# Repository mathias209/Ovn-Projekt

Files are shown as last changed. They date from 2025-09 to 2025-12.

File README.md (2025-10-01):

# Repo til vores ovnprojekt
beskrivelse go here

rapporter ligger i onedrive
rapport i word er her:
[Rapport](https://dtudk-my.sharepoint.com/:w:/r/personal/s256053_dtu_dk/Documents/Desktop/Projects/Ovn%20project.docx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)

[link til gruppe arbejde i Stens timer](https://github.com/mathias209/Elektroteknik-gruppearbejde)

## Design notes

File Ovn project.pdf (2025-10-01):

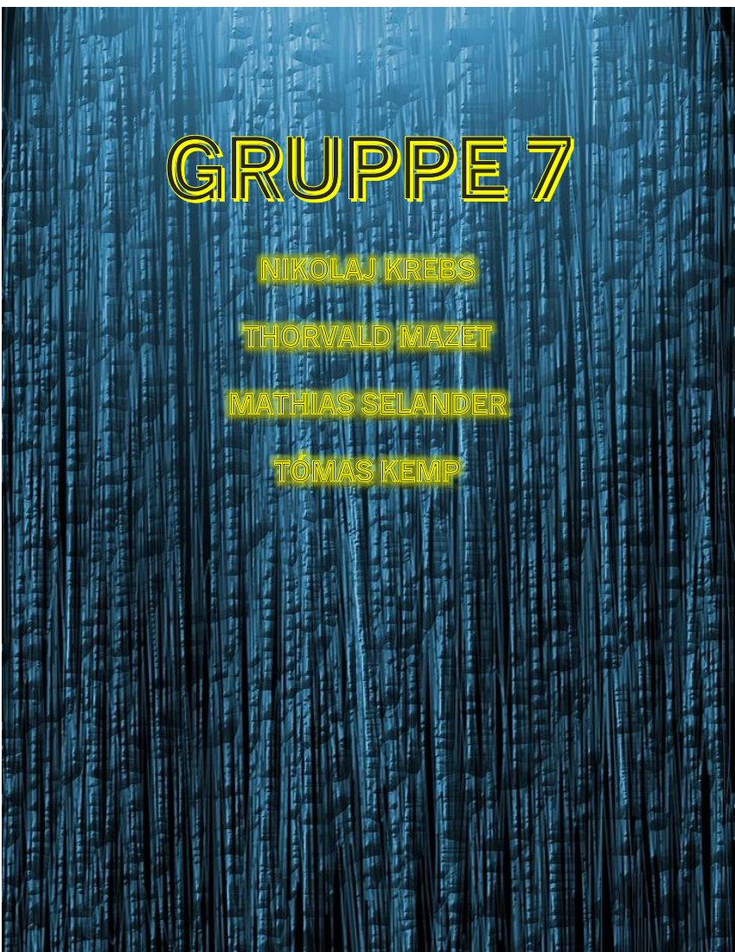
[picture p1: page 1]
01/10-2025 Gruppe 7

## Rapport for Digital Oscillator

# Contents

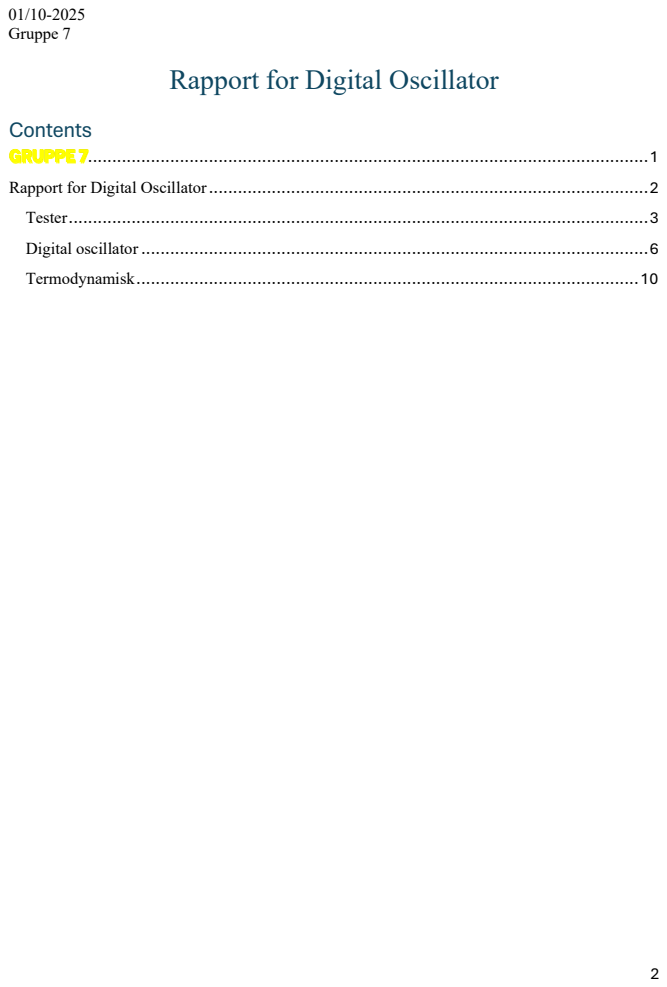
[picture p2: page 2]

## Tester

Tegn et lille diagram med en Light Emitting diode (LED) i serieforbindelse med en modstand.

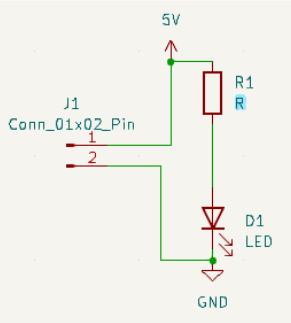
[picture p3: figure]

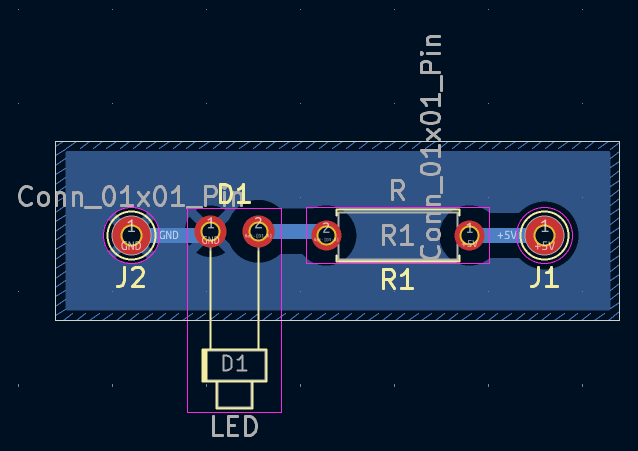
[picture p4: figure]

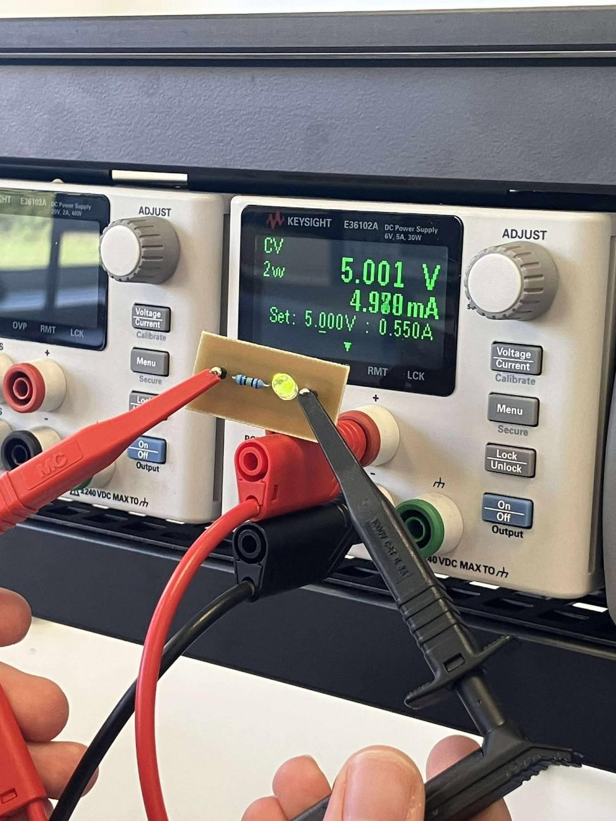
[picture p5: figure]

Iled = 5mA

VS = 5V

VR = 3V

R =

3V
0.005A

= 600Ω

Vi skal bruge en 600 ohm resistor.

## Digital oscillator

Vi skal lave et pcb-board med følgende kredsløb:

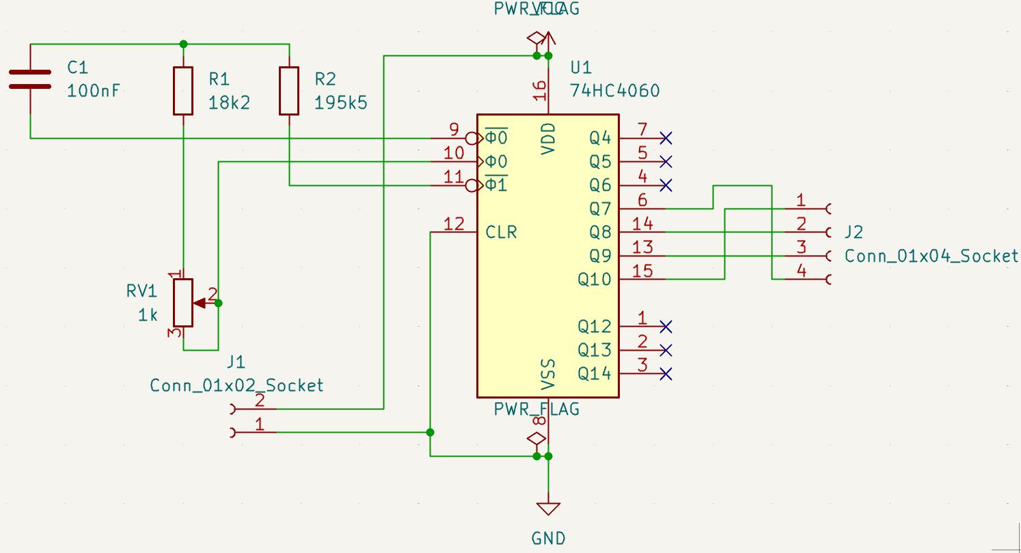
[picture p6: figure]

Vores færdige PCB kom så til at se sådan ud:

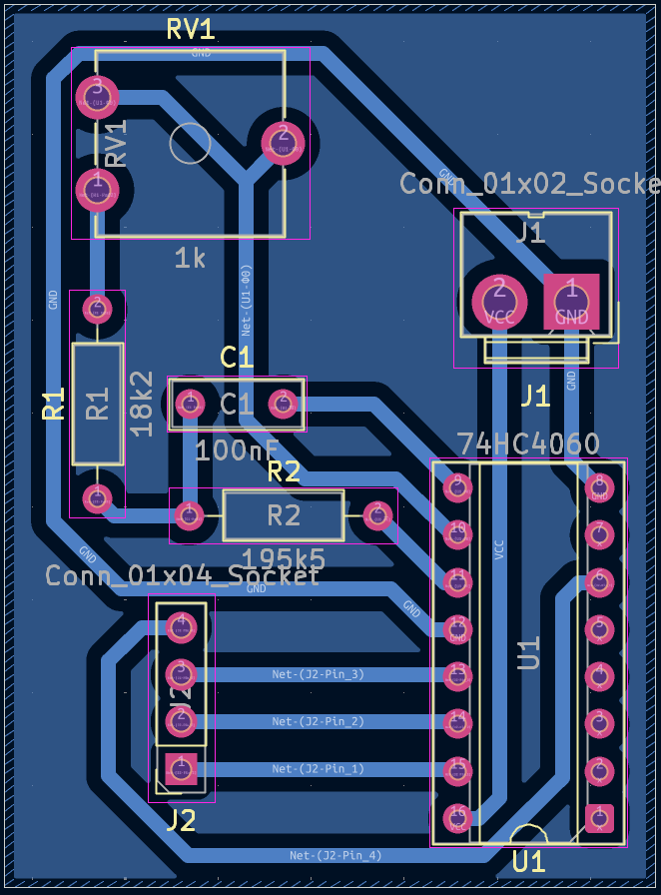
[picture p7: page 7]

Vi skulle udregne modstanden R1 så det var en indgangsfrekvens på 256Hz. Det gjorde vi med følgende formel:

1

Udregning i Maple:

I serie med modstanden skulle vi have et potentiometer så vi kunne justere vores modstand til at være så præcis så muligt. Den totale modstand skulle maksimalt være 10% højere en værdien som vi udregnet:

For at ramme de 17k8 ohm præcist, tilslutter vi en modstand på 17k2 ohm samt et potentiometer på 1k ohm.

Herefter har vi sat modstanden plus potentiometer gennem et multimeter og målt mens vi har drejet potentiometeret til at multimeteret viste 17k8 ohm.

Herefter tjekker vi frekvensen fra udgang Q8 gennem et ocsilloscop og ser en frekvens på 0.91 hz. Vores teori er at fejlen på 0.09hz sker pga. loddetin der virker som mindre capacitator.

1 Formel fra opgavebeskrivelse.

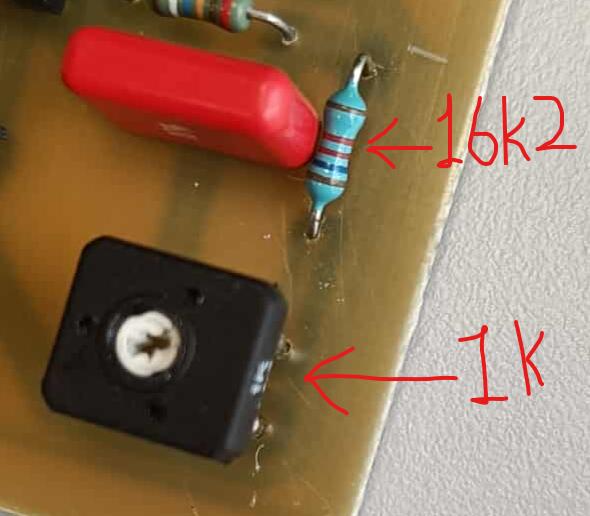
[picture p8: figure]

For at ramme vores ønskede frekvens på 1 hz ud fra udgang Q8, må vi derfor installere en mindre modstand i stedet for 17k2 ohm. Vi har ændret modstanden til at være 16k2 ohm. Vi har herefter drejet på potentiometeret til at vi får en frekvens på 0.99hz.

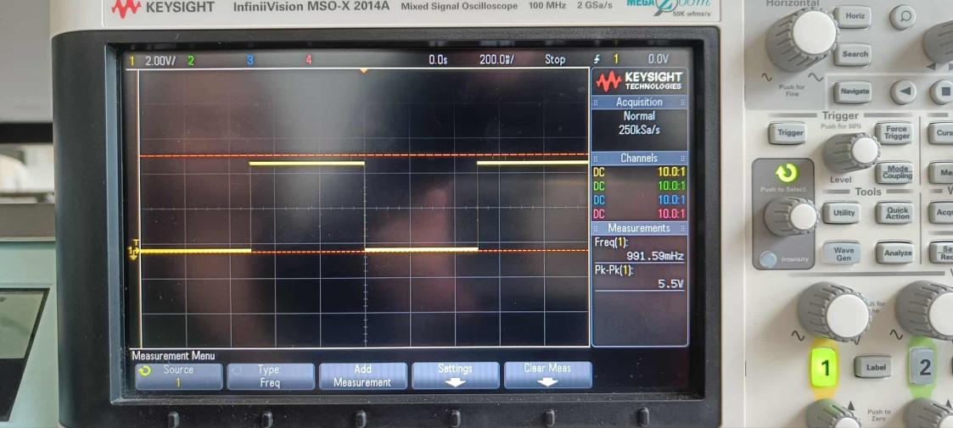
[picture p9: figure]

Herefter har vi målt på vores modstand gennem multimeter:

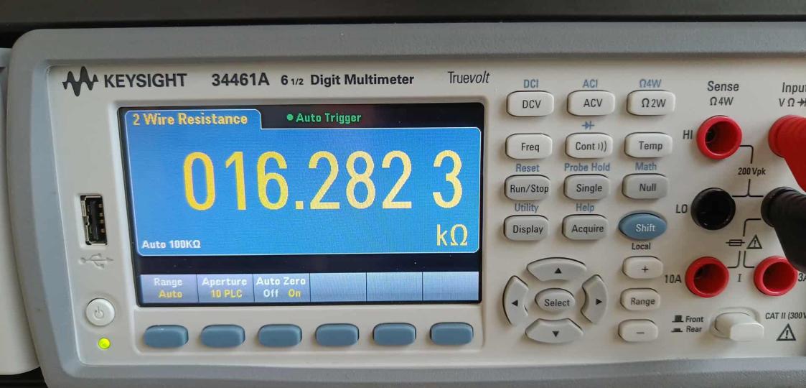
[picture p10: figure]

Her ser vi at vores samlede modstand R1 ligger på 16.28 kOhm.

## Termodynamisk

Vores udregning for R3 for henholdsvis 5W og 10W:

2

2

Screenshot af excel fil fra projektmappe.

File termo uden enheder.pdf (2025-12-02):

## Termodynamisk data

:

## Udregning af målt temp LM35DT

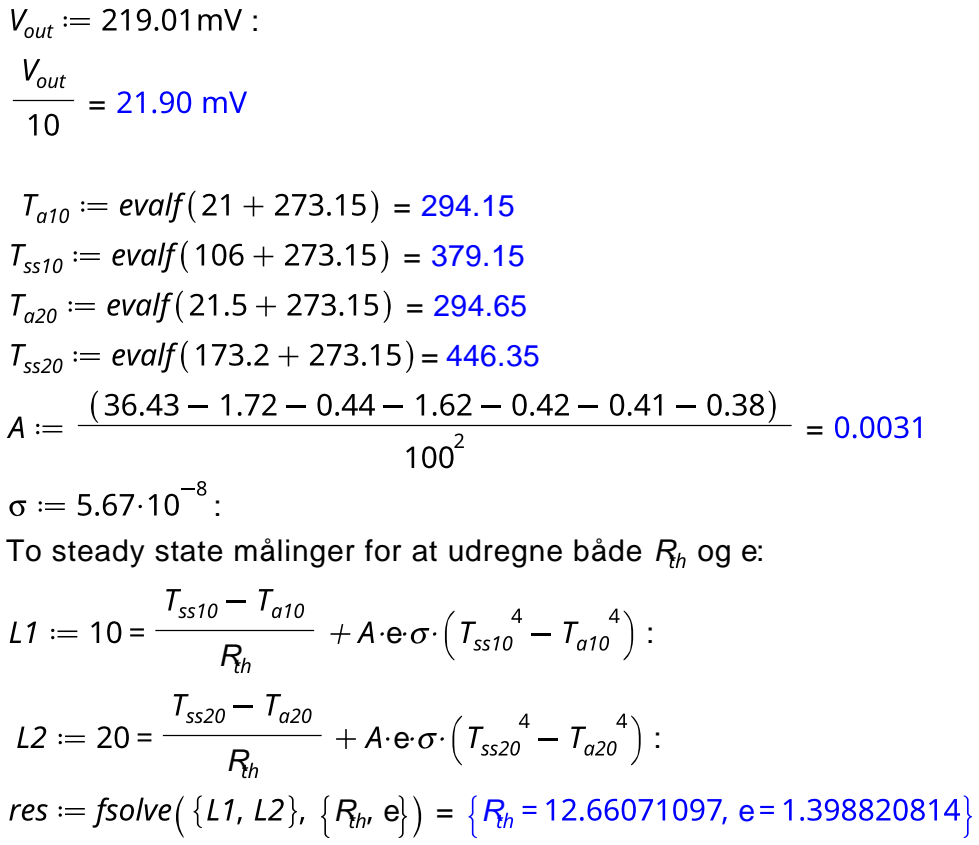
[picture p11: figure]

To steady state målinger for at udregne både R og e:

Siden e ikke mindst ikke har en passende værdi, den er ikke engang mellem 0 og 1. Derfor er det rimelig sikkert at gå ud fra at vores målinger ikke er præcise nok. Derfor antager vi en rimelig værdi for e på 0.25, og udregner en R for begge vores målinger og

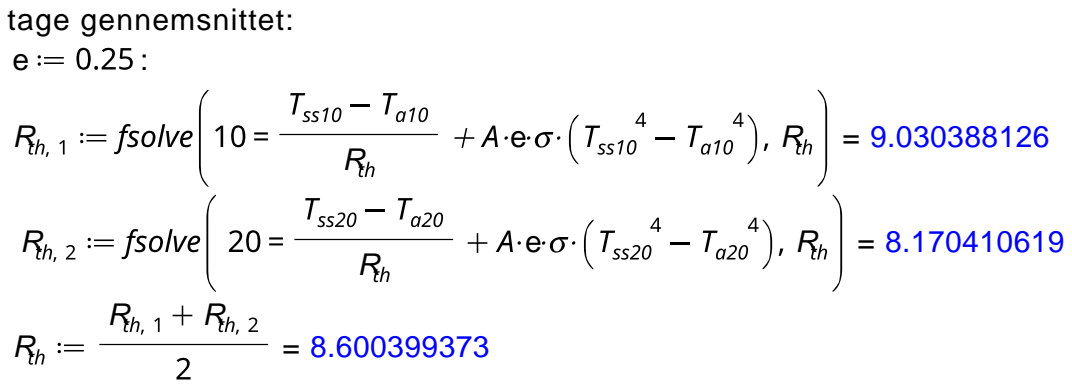
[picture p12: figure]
tage gennemsnittet:

## Cth

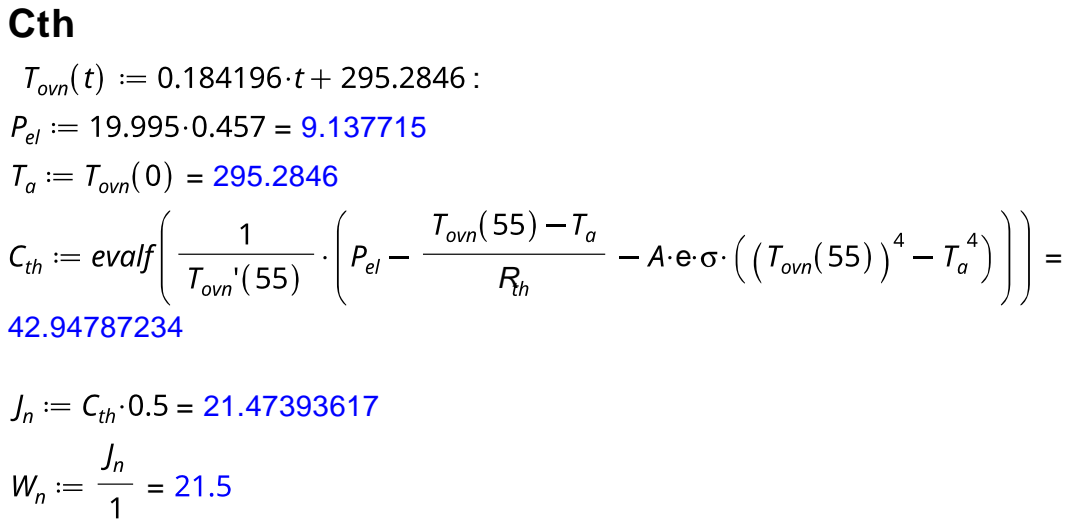
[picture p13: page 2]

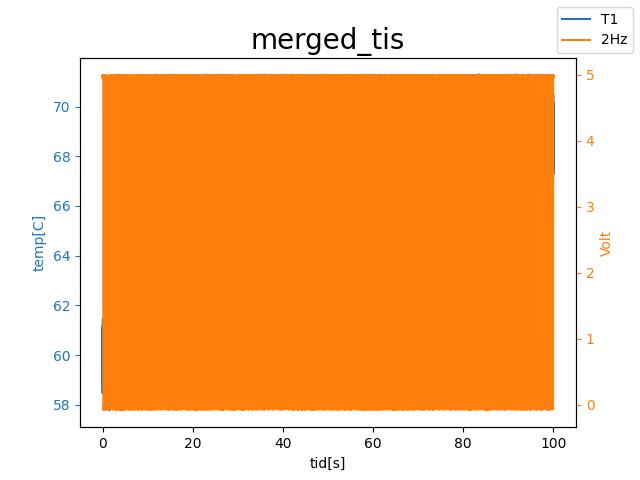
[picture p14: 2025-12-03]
python datahåndtering/merged_tis-out.jpg

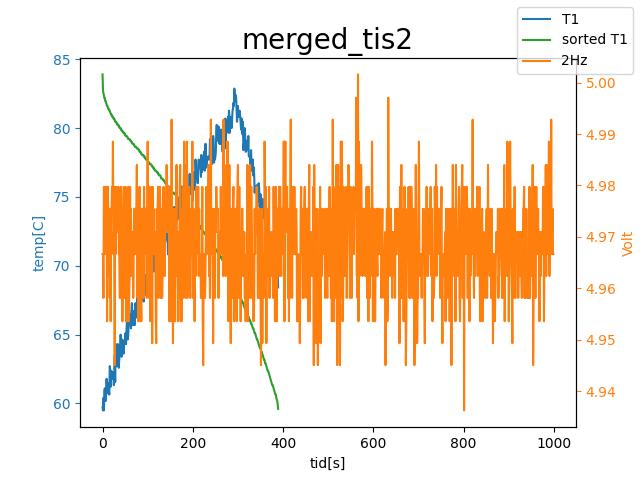
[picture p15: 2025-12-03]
python datahåndtering/merged_tis2-out.jpg

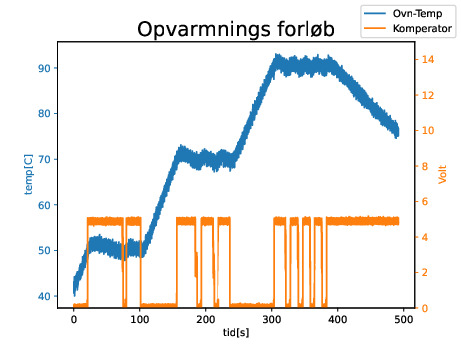
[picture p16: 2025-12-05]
python datahåndtering/Opvarmnings forløb.jpg

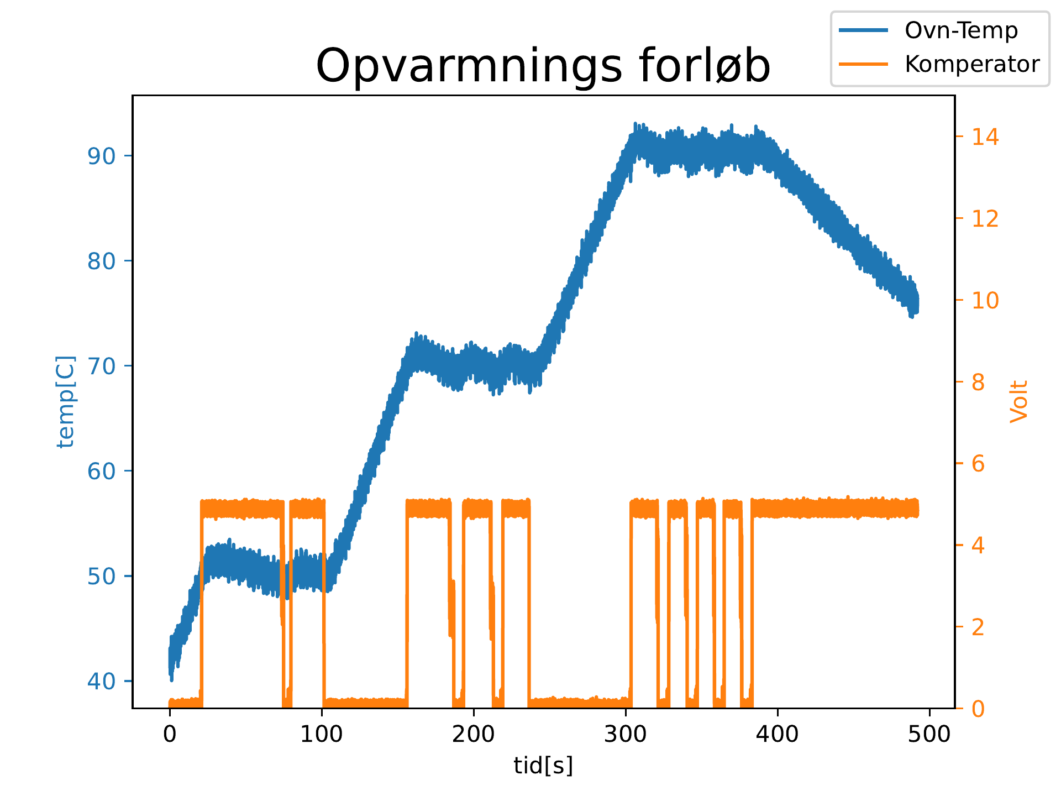
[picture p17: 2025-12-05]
python datahåndtering/output-1.png

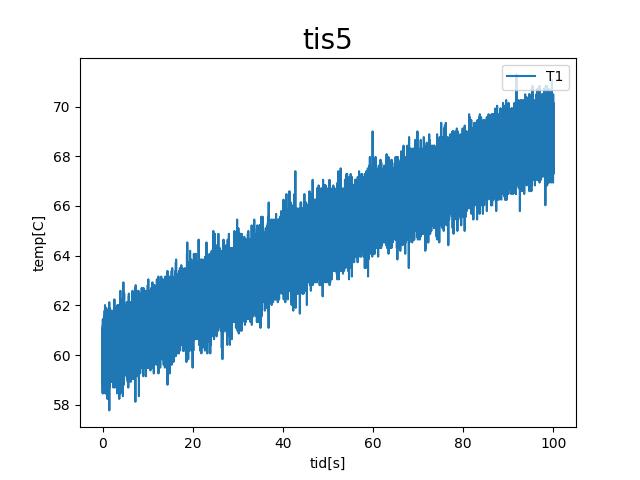
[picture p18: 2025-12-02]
python datahåndtering/tis5-out.jpg

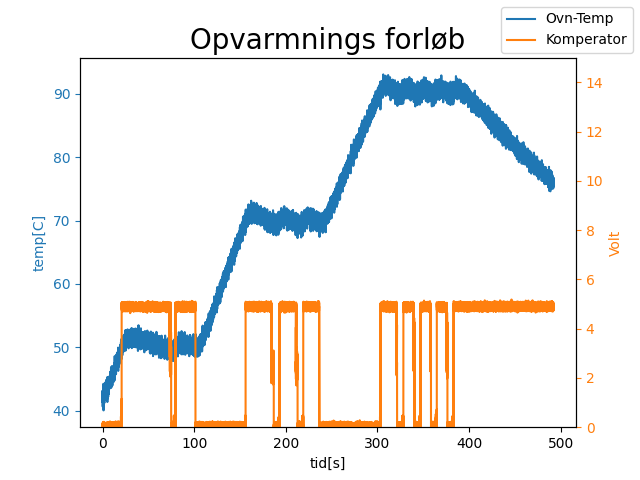
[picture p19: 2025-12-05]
python datahåndtering/Opvarmnings forløb.png

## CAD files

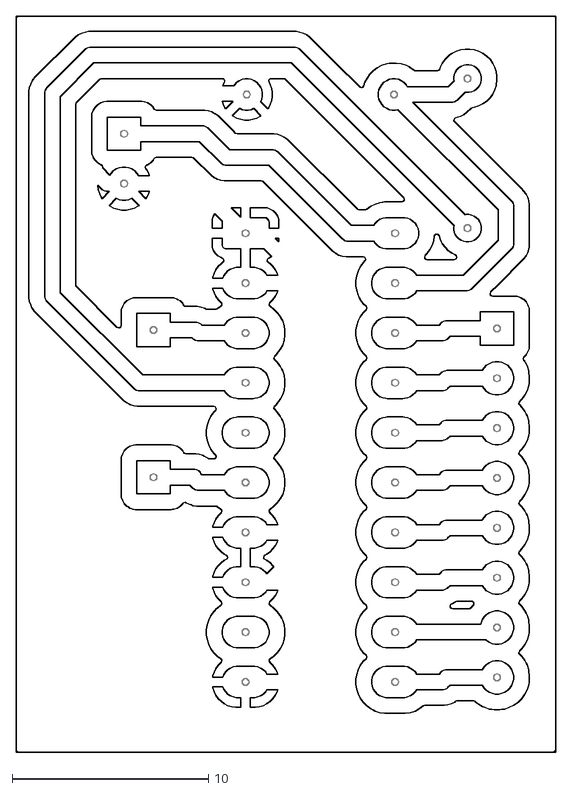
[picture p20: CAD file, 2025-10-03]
adc/ADC-B_Cu.dxf
27.5 x 37.5

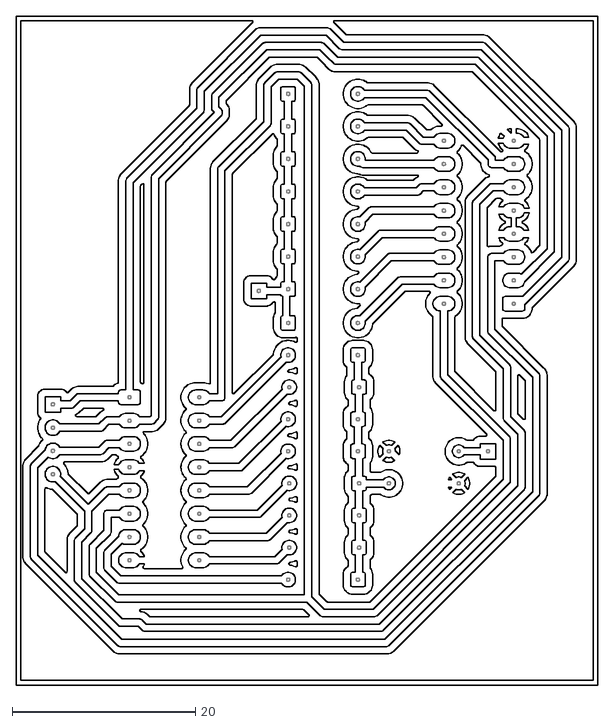
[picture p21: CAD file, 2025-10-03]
decoder/decoder-B_Cu.dxf
63.5 x 73.0

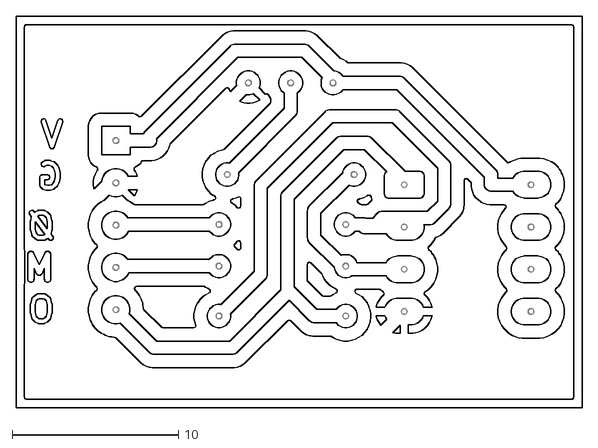
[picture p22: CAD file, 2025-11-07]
Differens forstærker/Differens forstærker-B_Cu.dxf
34.0 x 23.5

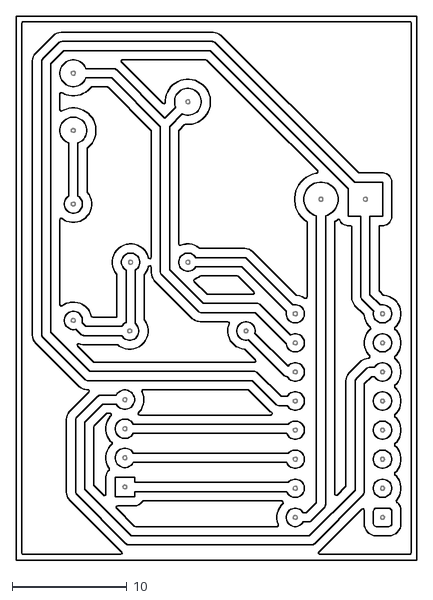
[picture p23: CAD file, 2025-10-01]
digital oscilatoropgave 2/digital oscilatoropgave 2-B_Cu.dxf
35.0 x 47.5

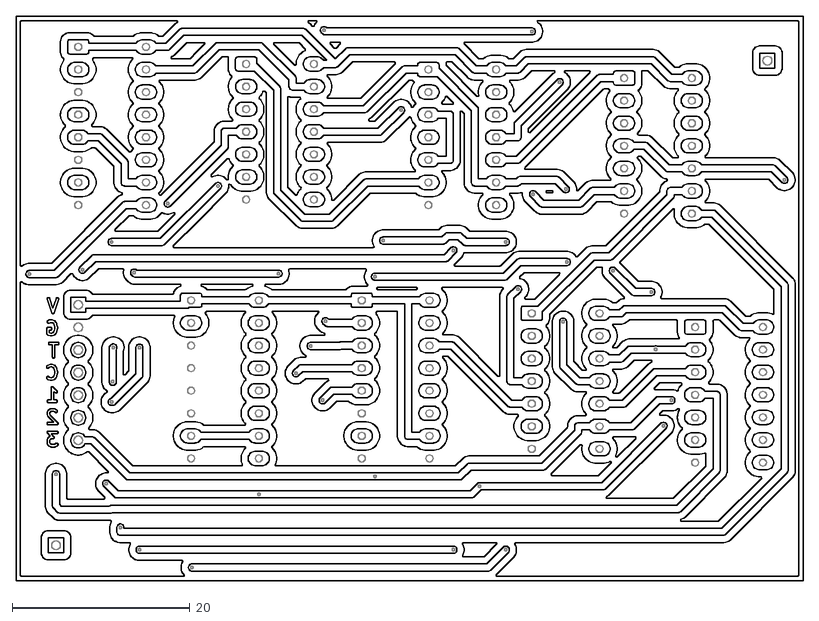
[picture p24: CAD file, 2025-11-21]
digital styring/digital styring-B_Cu.dxf
88.5 x 63.5

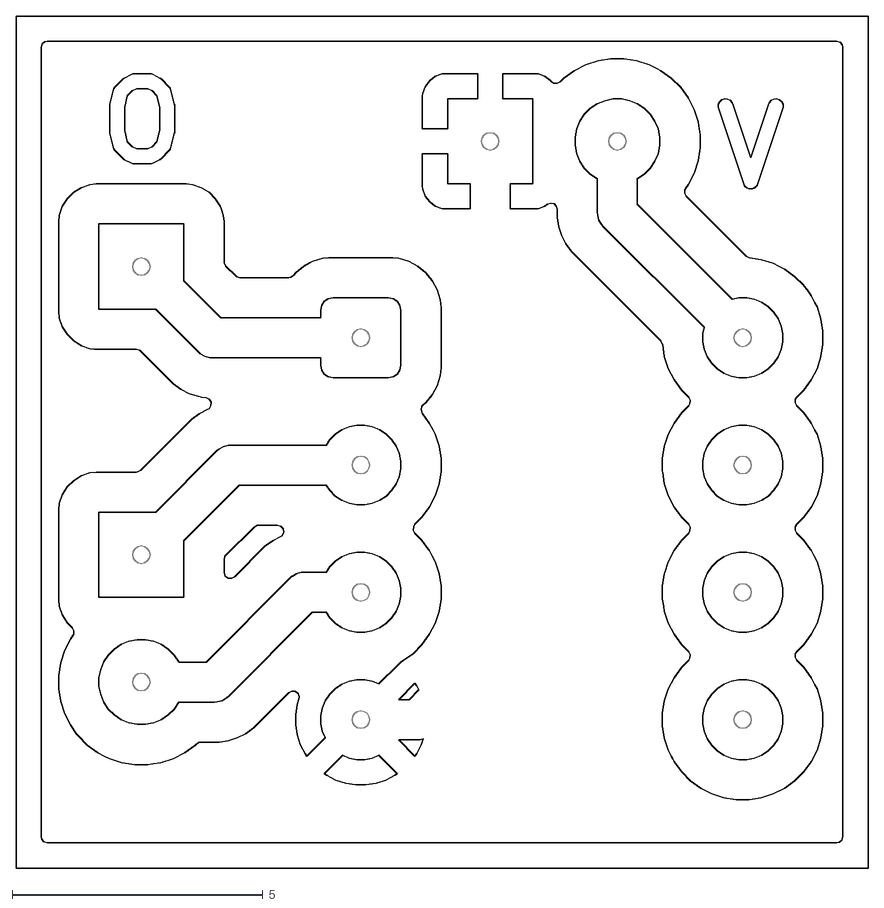
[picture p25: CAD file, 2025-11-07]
Komparator/komparator-B_Cu.dxf
17.0 x 17.0

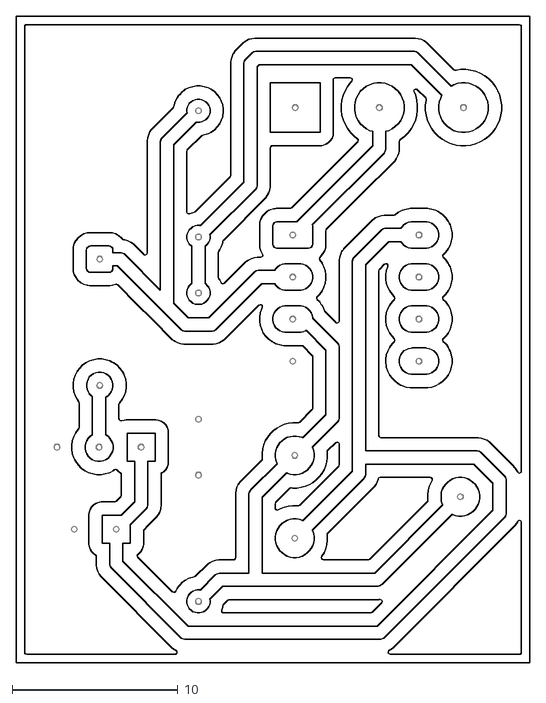
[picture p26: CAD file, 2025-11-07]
Måling af termodynamisk data/Måling af termodynamisk data-B_Cu.dxf
31.0 x 39.0

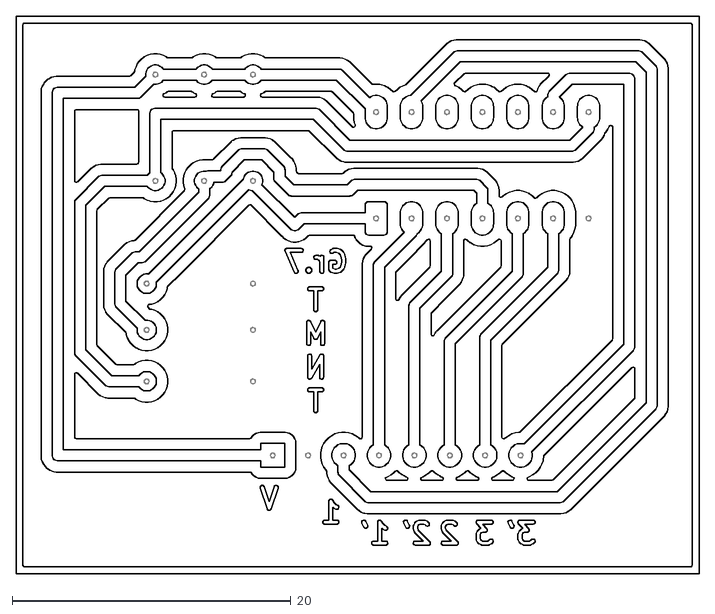
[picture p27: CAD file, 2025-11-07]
Spændingsdeler multiplexer/Spændingsdeler multiplexer-B_Cu.dxf
49.0 x 40.0

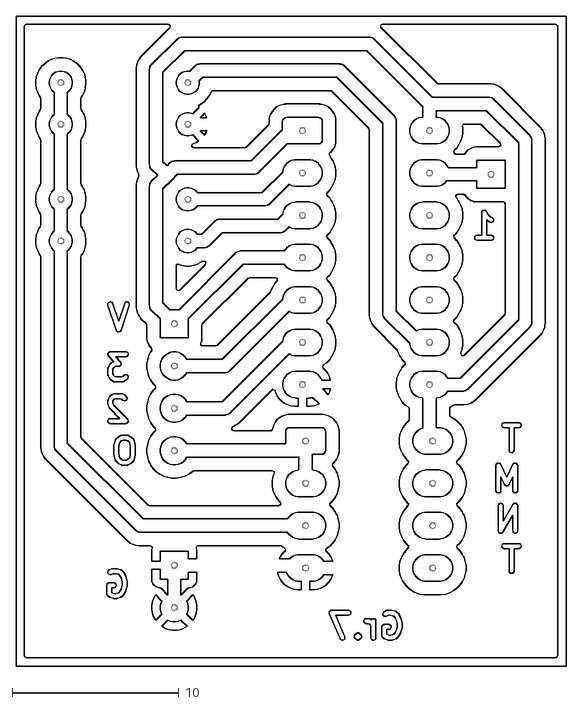
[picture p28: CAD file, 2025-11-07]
Spændingsdeler/Spændingsdeler-B_Cu.dxf
33.0 x 39.0

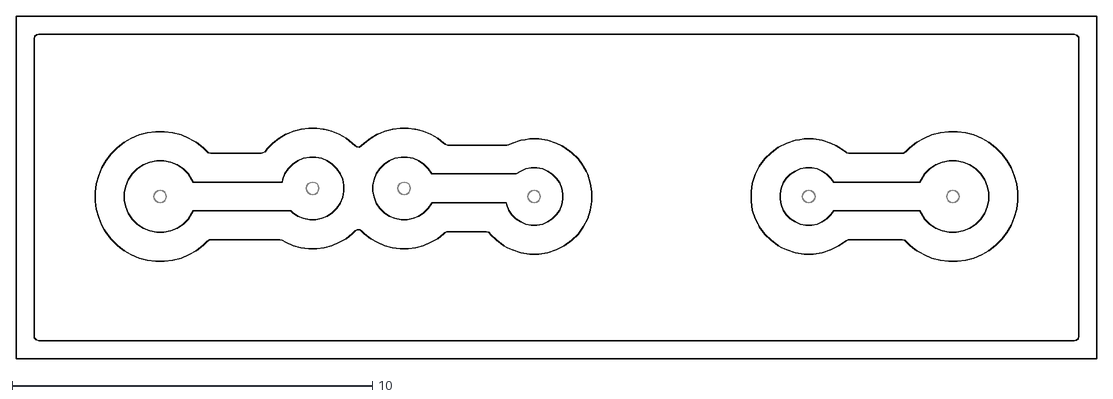
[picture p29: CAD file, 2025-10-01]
tester/tester-B_Cu.dxf
30.0 x 9.50

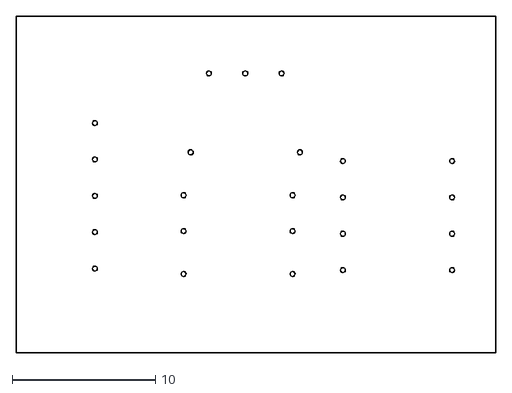
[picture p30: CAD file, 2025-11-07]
Differens forstærker/Differens forstærker-Edge_Cuts.dxf
33.5 x 23.5

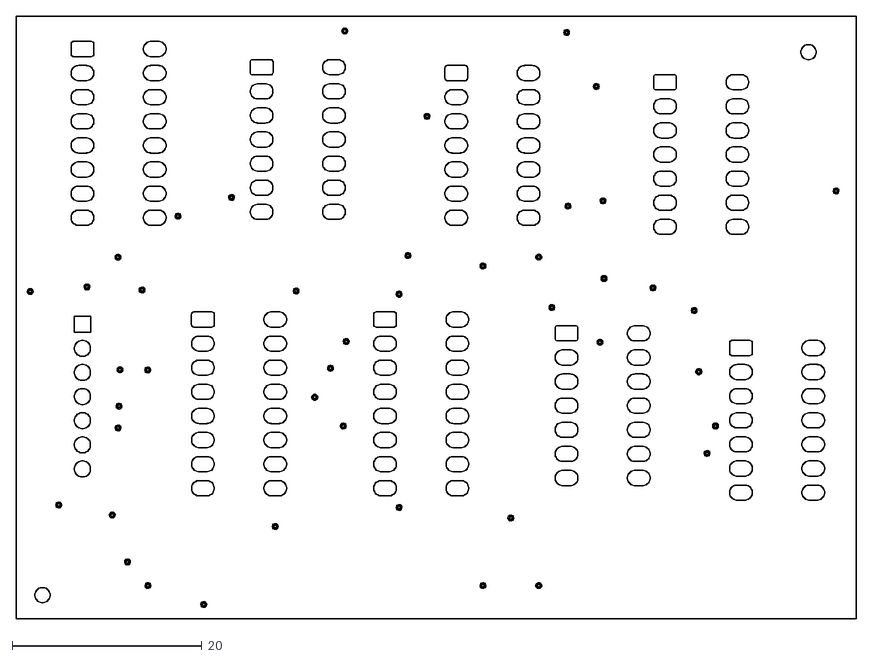
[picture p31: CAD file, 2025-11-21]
digital styring/digital styring-In1_Cu.dxf
88.5 x 63.5

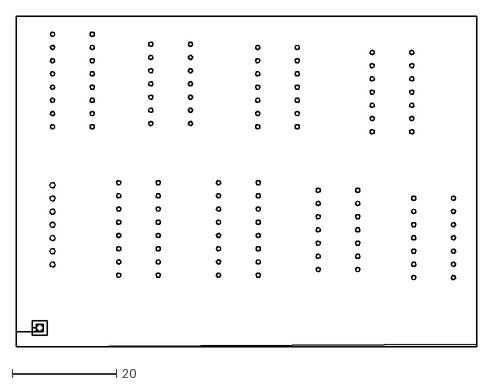
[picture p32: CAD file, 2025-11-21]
digital styring/digital styring-User_Comments.dxf
88.5 x 63.5

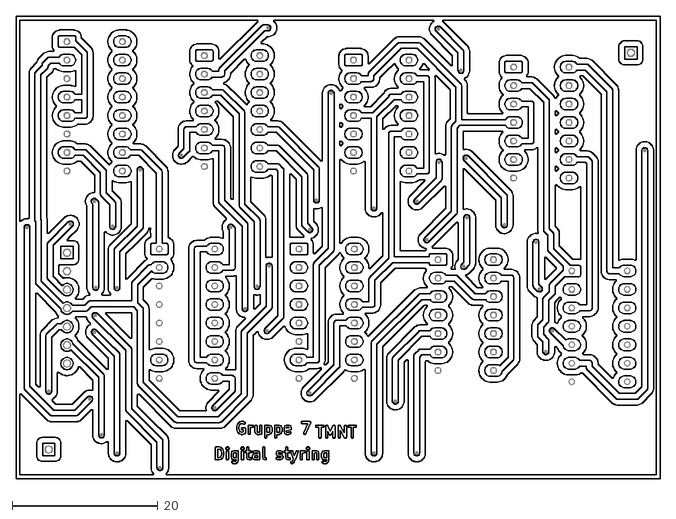
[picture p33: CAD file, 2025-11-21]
digital styring/digital styring-F_Cu.dxf
88.5 x 63.5

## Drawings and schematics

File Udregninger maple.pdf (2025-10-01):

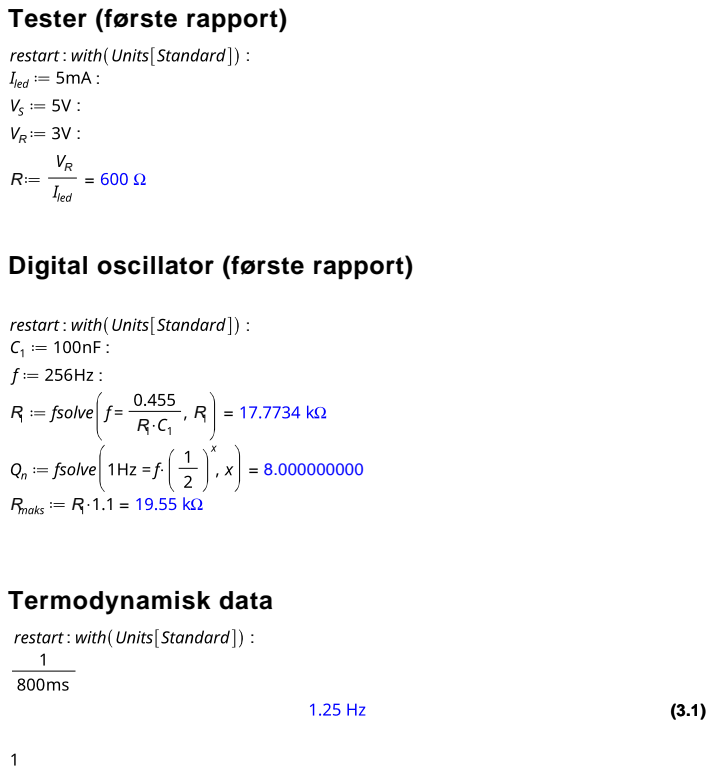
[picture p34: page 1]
Termodynamisk data

Tester (første rapport)

Digital oscillator (første rapport)

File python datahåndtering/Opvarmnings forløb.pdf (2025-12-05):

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

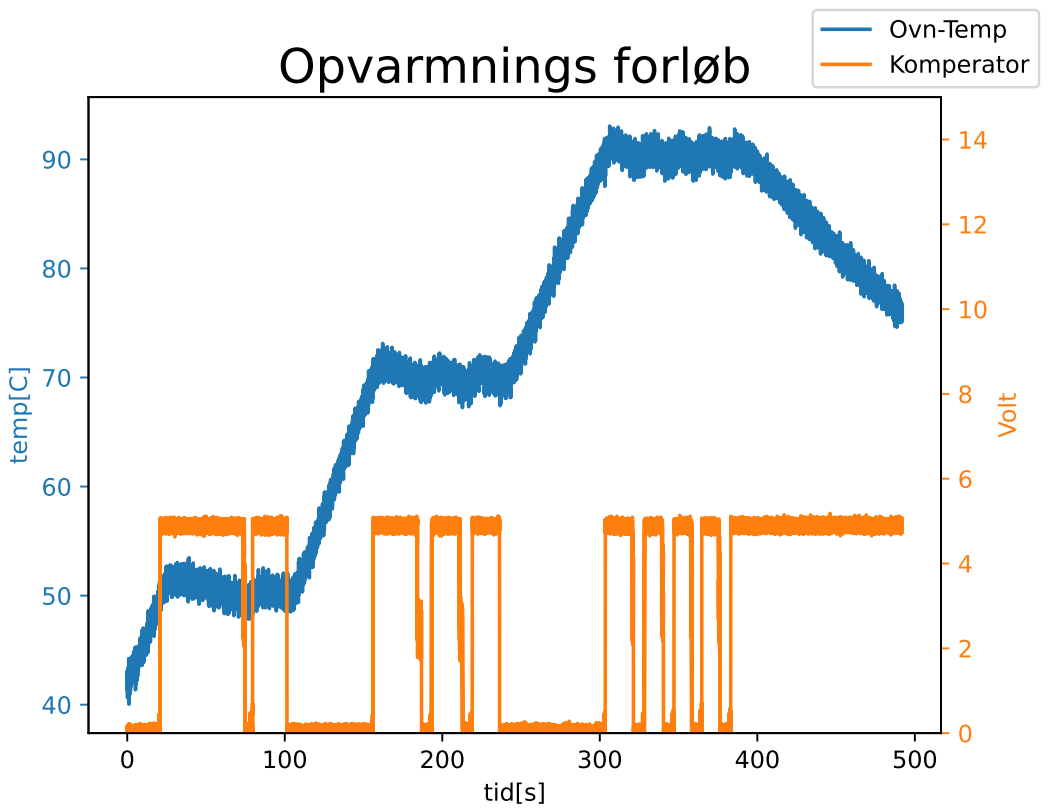
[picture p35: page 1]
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

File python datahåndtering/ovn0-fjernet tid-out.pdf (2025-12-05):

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

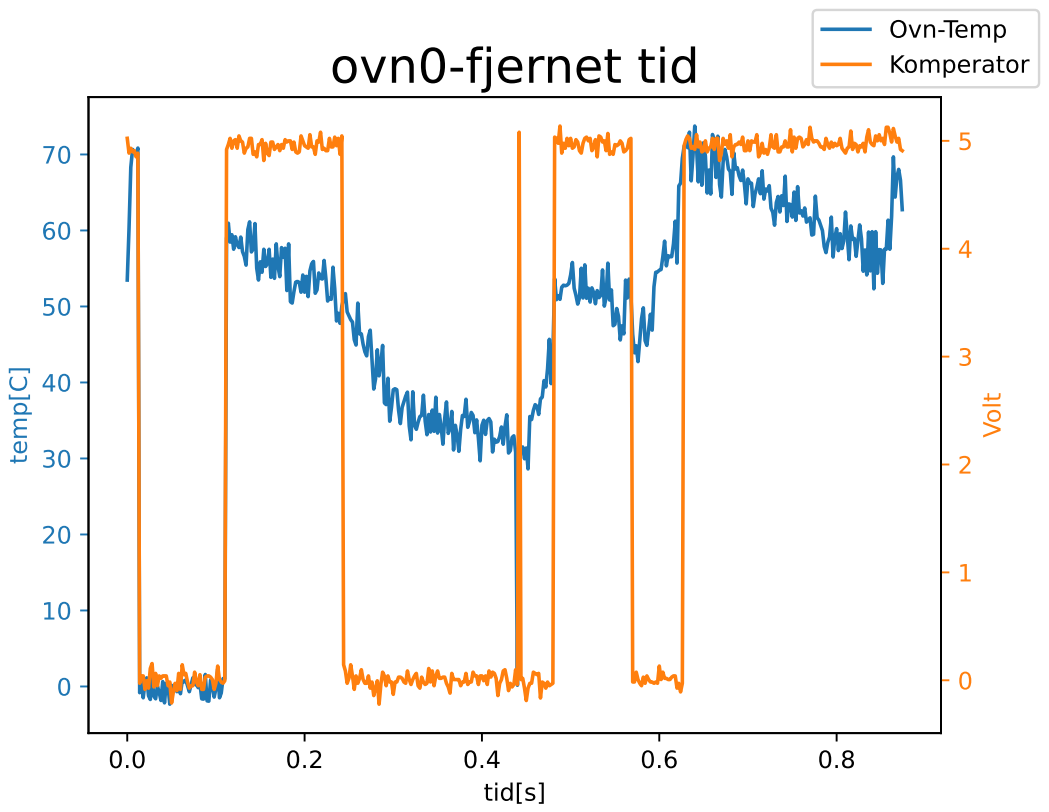
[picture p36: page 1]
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

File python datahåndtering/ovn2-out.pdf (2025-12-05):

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

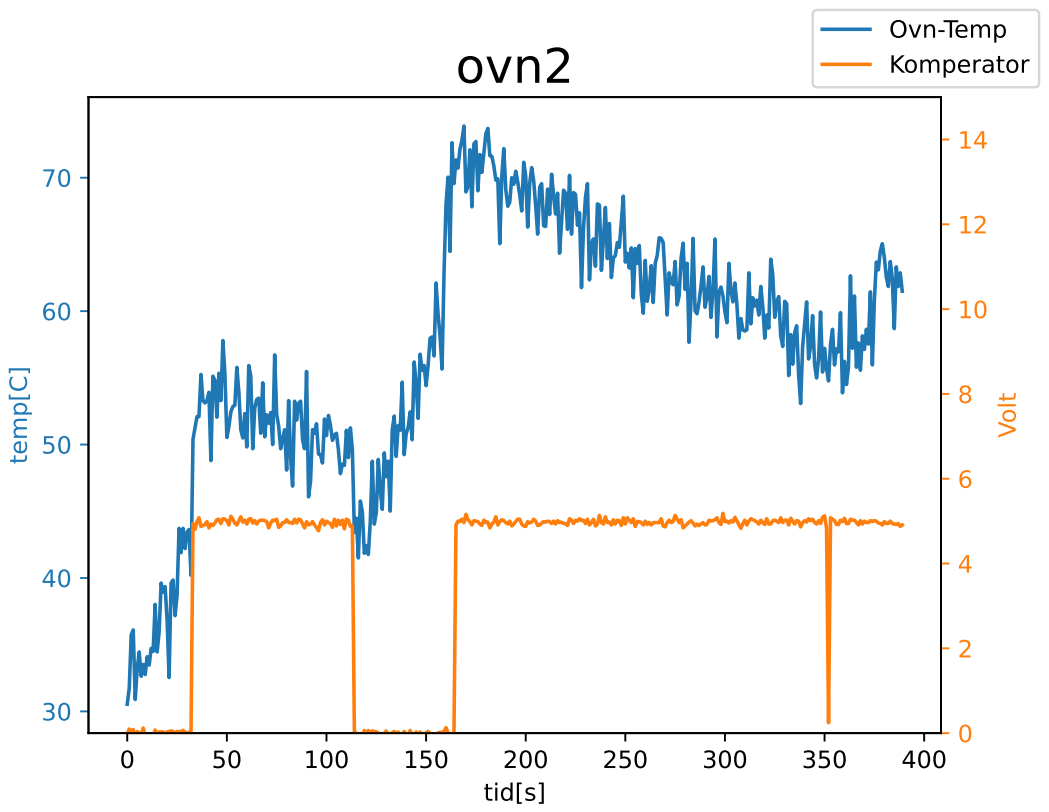
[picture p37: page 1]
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

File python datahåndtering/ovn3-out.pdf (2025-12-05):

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

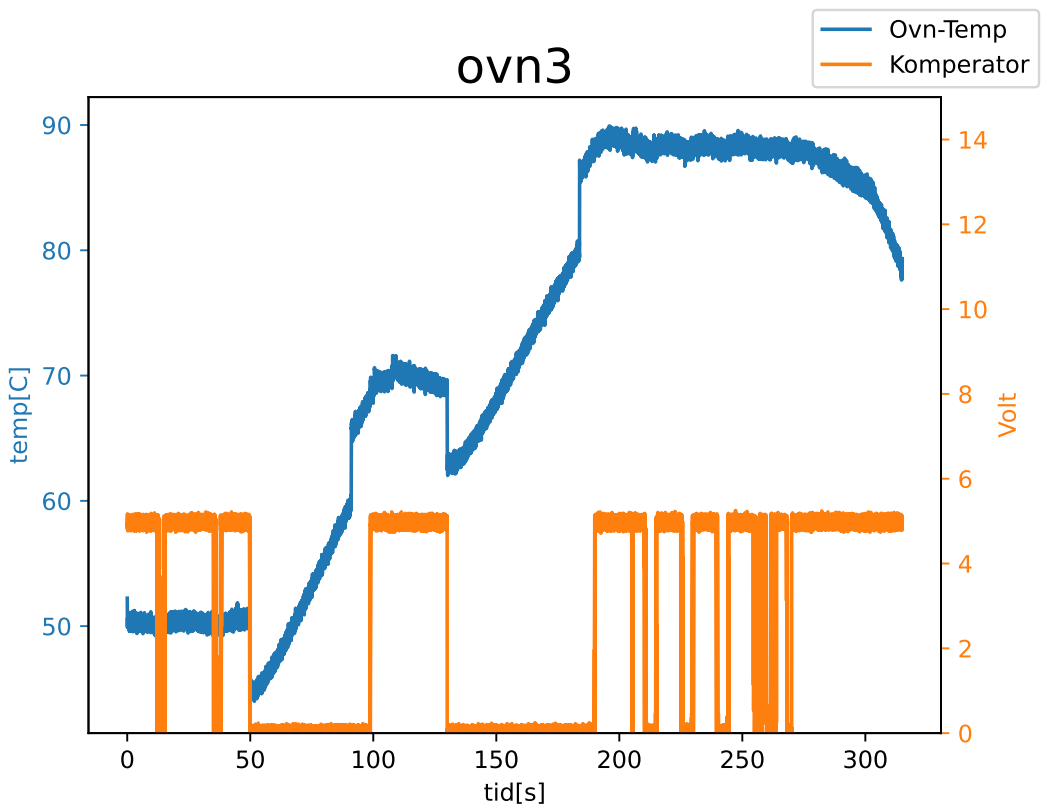
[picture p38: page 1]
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

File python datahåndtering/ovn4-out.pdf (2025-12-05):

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

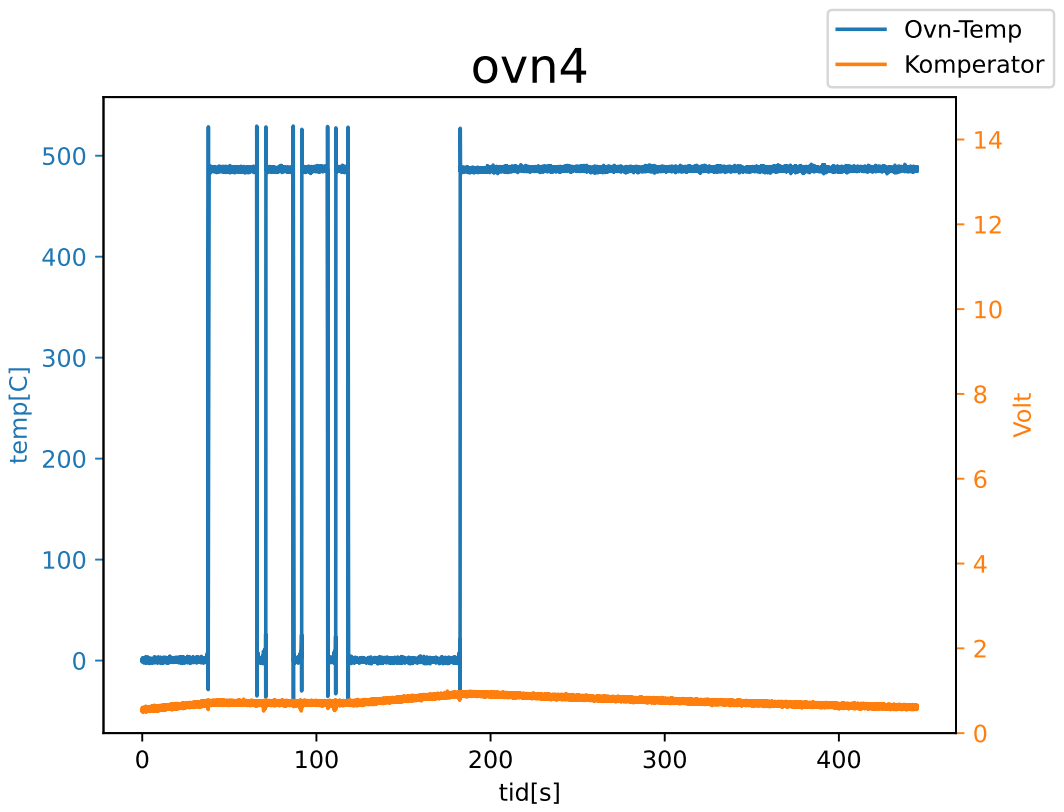
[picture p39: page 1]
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

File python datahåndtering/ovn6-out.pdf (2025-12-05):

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

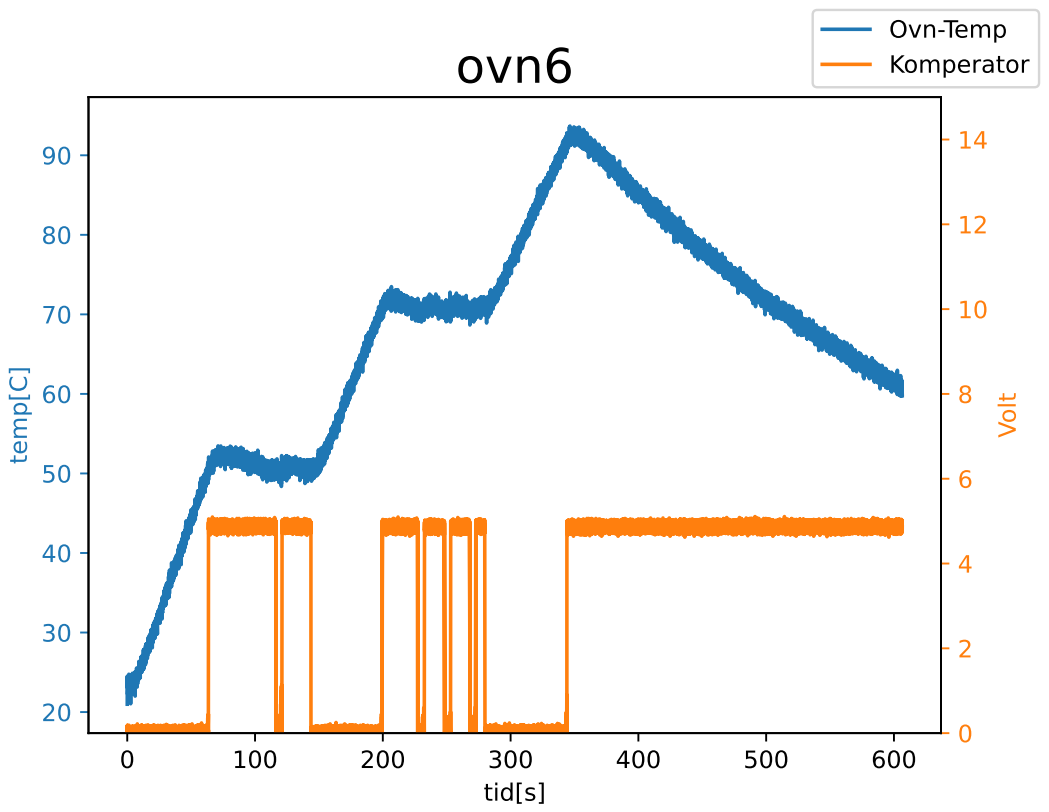
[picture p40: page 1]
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

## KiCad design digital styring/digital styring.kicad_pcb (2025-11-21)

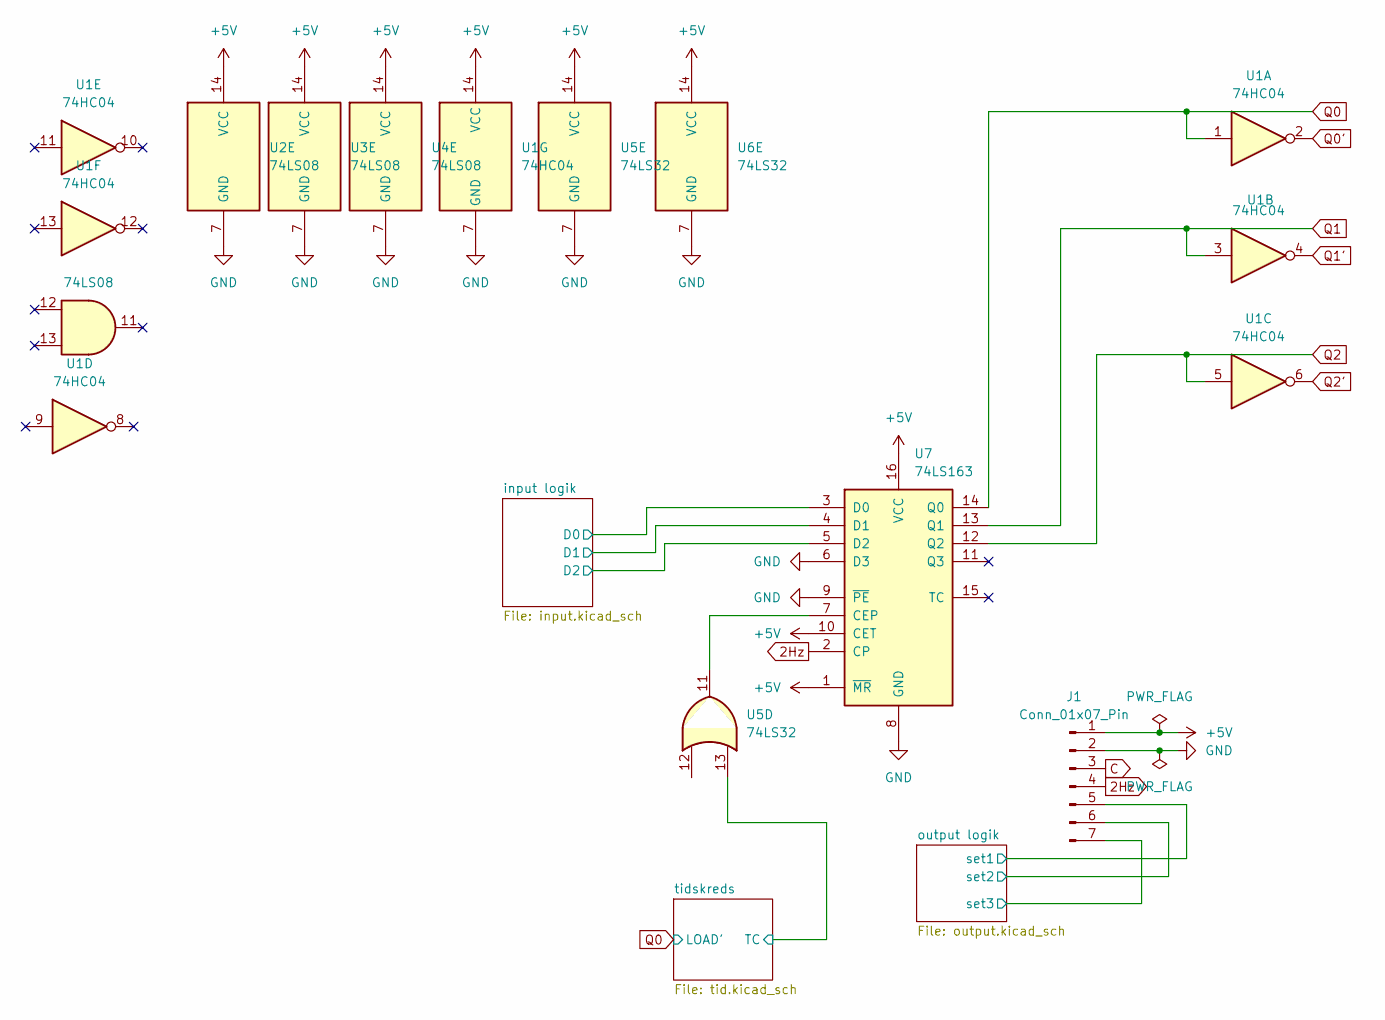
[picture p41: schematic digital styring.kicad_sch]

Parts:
J1: Conn_01x07_Pin; PinSocket_1x07_P2.54mm_Vertical
U1: 74HC04; DIP-14_W7.62mm_LongPads
U2, U3, U4: 74LS08; DIP-14_W7.62mm_LongPads
U5, U6: 74LS32; DIP-14_W7.62mm_LongPads
U7: 74LS163; DIP-16_W7.62mm_LongPads

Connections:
2Hz: J1.4, U7.2 (CP); also elsewhere on the board
+5V: J1.1, U1.14 (VCC), U2.14 (VCC), U3.14 (VCC), U4.14 (VCC), U5.14 (VCC), U6.14 (VCC), U7.1 (~MR), U7.10 (CET), U7.16 (VCC); also elsewhere on the board
/input logik/D0: U7.3 (D0); also elsewhere on the board
/input logik/D1: U7.4 (D1); also elsewhere on the board
/input logik/D2: U7.5 (D2); also elsewhere on the board
/output logik/set2: J1.6; also elsewhere on the board
/tidskreds/TC: U5.13; also elsewhere on the board
C: J1.3; also elsewhere on the board
GND: J1.2, U1.7 (GND), U2.7 (GND), U3.7 (GND), U4.7 (GND), U5.7 (GND), U6.7 (GND), U7.6 (D3), U7.8 (GND), U7.9 (~PE); also elsewhere on the board
unnamed: U5.11, U7.7 (CEP)
Q0: U1.1, U7.14 (Q0); also elsewhere on the board
Q0': U1.2, U5.12; also elsewhere on the board
Q1: U1.3, U7.13 (Q1); also elsewhere on the board
Q1': J1.5, U1.4
Q2: J1.7, U1.5, U7.12 (Q2); also elsewhere on the board
Q2': U1.6; also elsewhere on the board

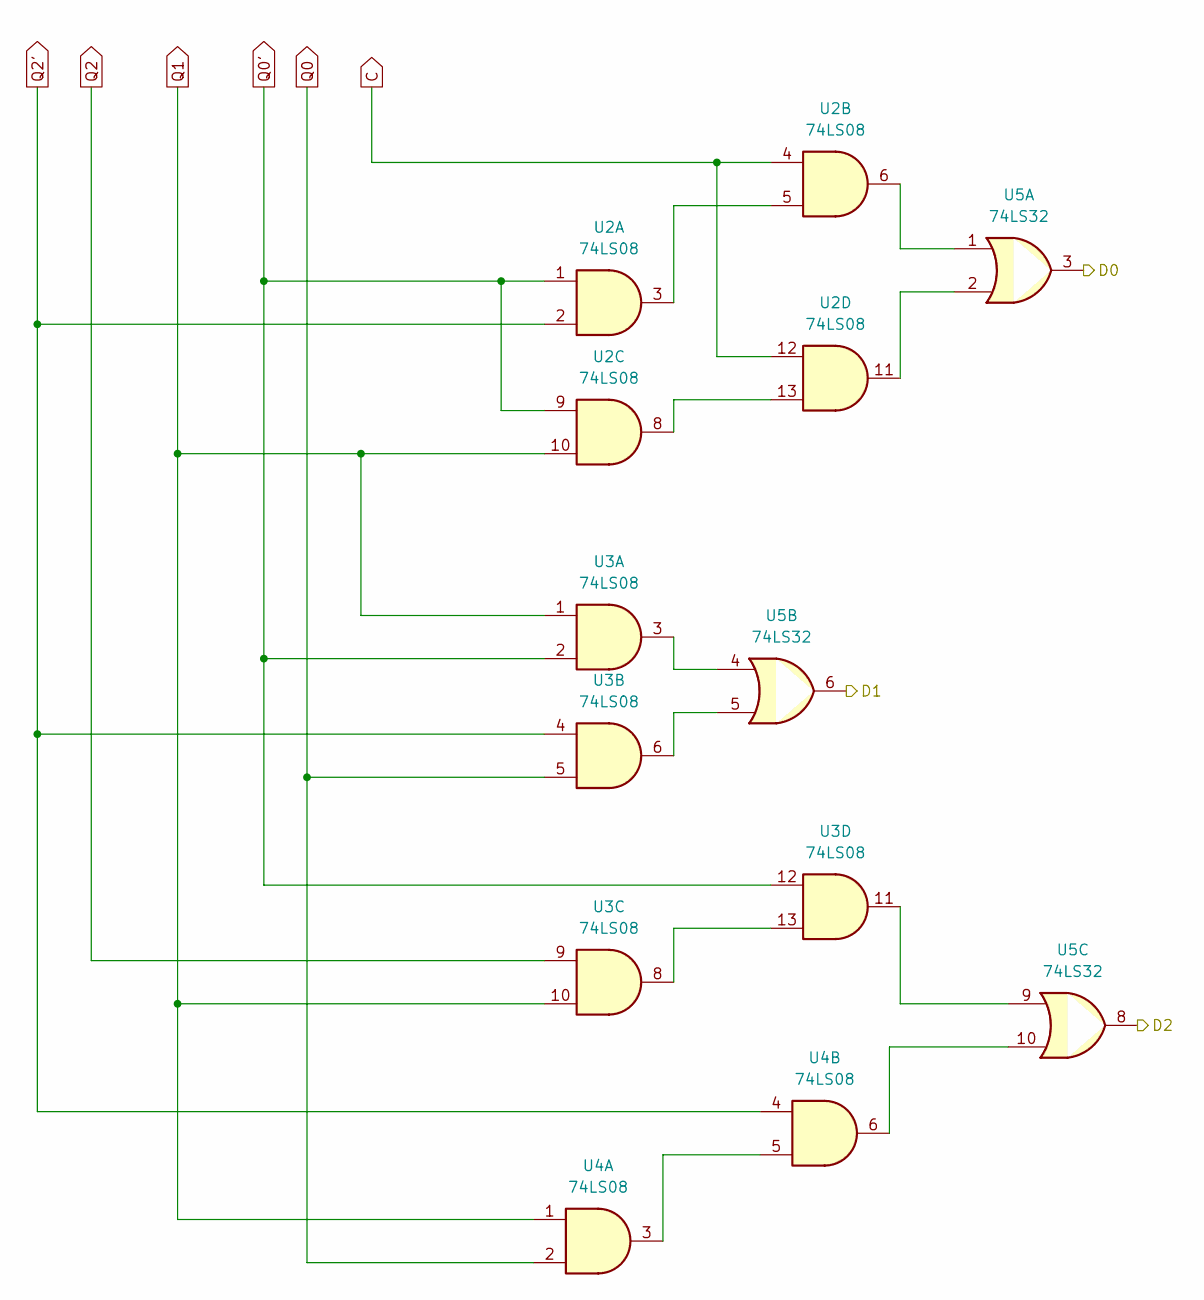
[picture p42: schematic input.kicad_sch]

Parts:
U2, U3, U4: 74LS08; DIP-14_W7.62mm_LongPads
U5: 74LS32; DIP-14_W7.62mm_LongPads

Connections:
/input logik/D0: U5.3; also elsewhere on the board
/input logik/D1: U5.6; also elsewhere on the board
/input logik/D2: U5.8; also elsewhere on the board
C: U2.4, U2.12; also elsewhere on the board
unnamed: U2.3, U2.5
unnamed: U2.6, U5.1
unnamed: U2.11, U5.2
unnamed: U2.8, U2.13
unnamed: U3.3, U5.4
unnamed: U3.6, U5.5
unnamed: U3.11, U5.9
unnamed: U3.8, U3.13
unnamed: U4.3, U4.5
unnamed: U4.6, U5.10
Q0: U3.5, U4.2; also elsewhere on the board
Q0': U2.1, U2.9, U3.2, U3.12; also elsewhere on the board
Q1: U2.10, U3.1, U3.10, U4.1; also elsewhere on the board
Q2: U3.9; also elsewhere on the board
Q2': U2.2, U3.4, U4.4; also elsewhere on the board

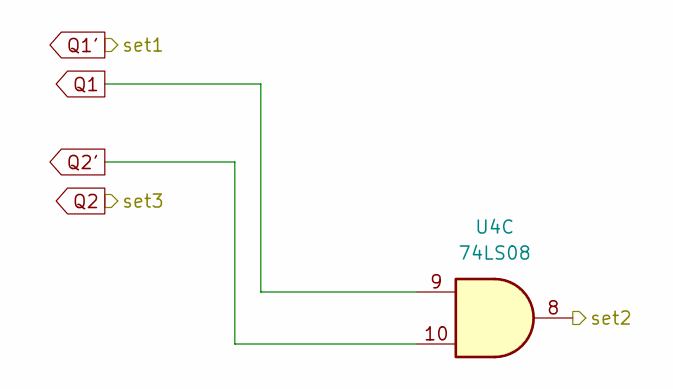
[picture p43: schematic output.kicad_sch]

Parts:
U4: 74LS08; DIP-14_W7.62mm_LongPads

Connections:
/output logik/set2: U4.8; also elsewhere on the board
Q1: U4.9; also elsewhere on the board
Q2': U4.10; also elsewhere on the board

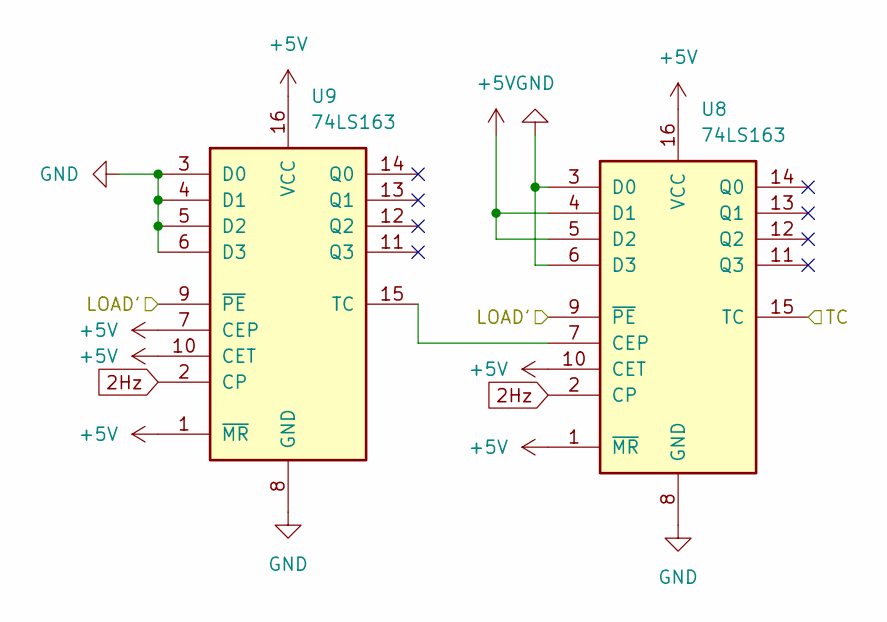
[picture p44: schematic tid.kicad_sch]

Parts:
U8, U9: 74LS163; DIP-16_W7.62mm_LongPads

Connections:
2Hz: U8.2 (CP), U9.2 (CP); also elsewhere on the board
+5V: U8.1 (~MR), U8.4 (D1), U8.5 (D2), U8.10 (CET), U8.16 (VCC), U9.1 (~MR), U9.7 (CEP), U9.10 (CET), U9.16 (VCC); also elsewhere on the board
/tidskreds/TC: U8.15 (TC); also elsewhere on the board
GND: U8.3 (D0), U8.6 (D3), U8.8 (GND), U9.3 (D0), U9.4 (D1), U9.5 (D2), U9.6 (D3), U9.8 (GND); also elsewhere on the board
unnamed: U8.7 (CEP), U9.15 (TC)
Q0: U8.9 (~PE), U9.9 (~PE); also elsewhere on the board

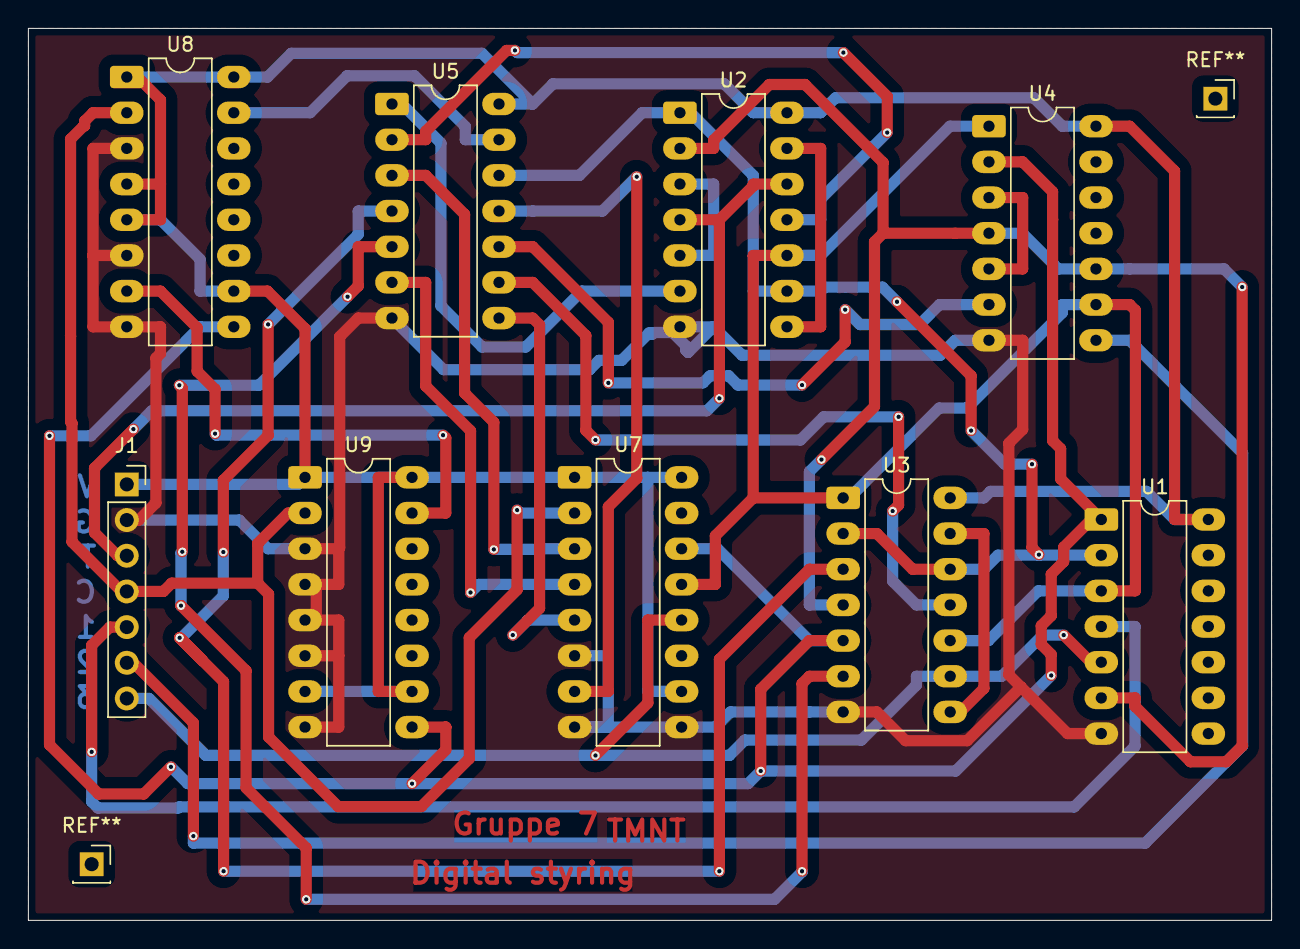
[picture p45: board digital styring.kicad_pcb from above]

Board: 2 copper layers, 88.5 x 63.5 mm, 9 parts (0 on the bottom side), 27 nets.

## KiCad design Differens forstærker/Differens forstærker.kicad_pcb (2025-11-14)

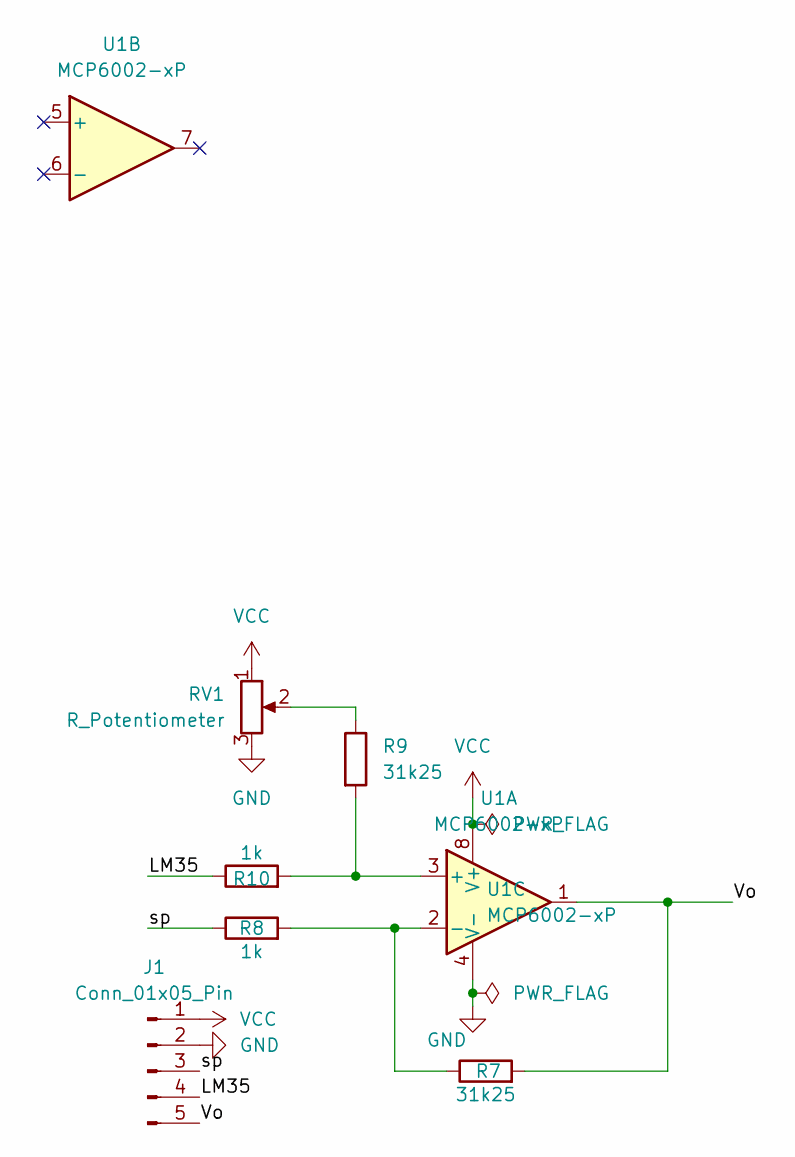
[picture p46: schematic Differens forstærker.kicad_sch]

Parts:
J1: Conn_01x05_Pin; PinSocket_1x05_P2.54mm_Vertical
R7, R9: 31k25; R_Axial_DIN0204_L3.6mm_D1.6mm_P7.62mm_Horizontal
R8, R10: 1k; R_Axial_DIN0204_L3.6mm_D1.6mm_P7.62mm_Horizontal
RV1: R_Potentiometer; Potentiometer_Bourns_3296W_Vertical
U1: MCP6002-xP; DIP-8_W7.62mm_LongPads

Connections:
/LM35: J1.4, R10.1
/Vo: J1.5, R7.2, U1.1
/sp: J1.3, R8.1
GND: J1.2, RV1.3, U1.4 (V-)
unnamed: R9.1, RV1.2
unnamed: R9.2, R10.2, U1.3 (+)
unnamed: R7.1, R8.2, U1.2 (-)
VCC: J1.1, RV1.1, U1.8 (V+)

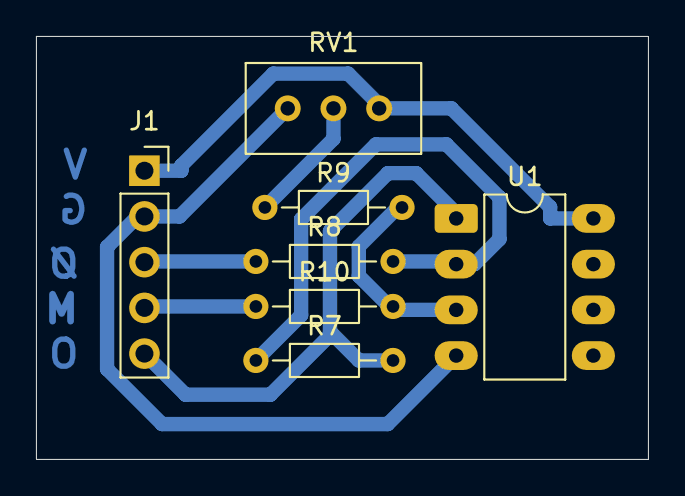
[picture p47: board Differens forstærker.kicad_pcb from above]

Board: 2 copper layers, 34.0 x 23.5 mm, 7 parts (0 on the bottom side), 8 nets.

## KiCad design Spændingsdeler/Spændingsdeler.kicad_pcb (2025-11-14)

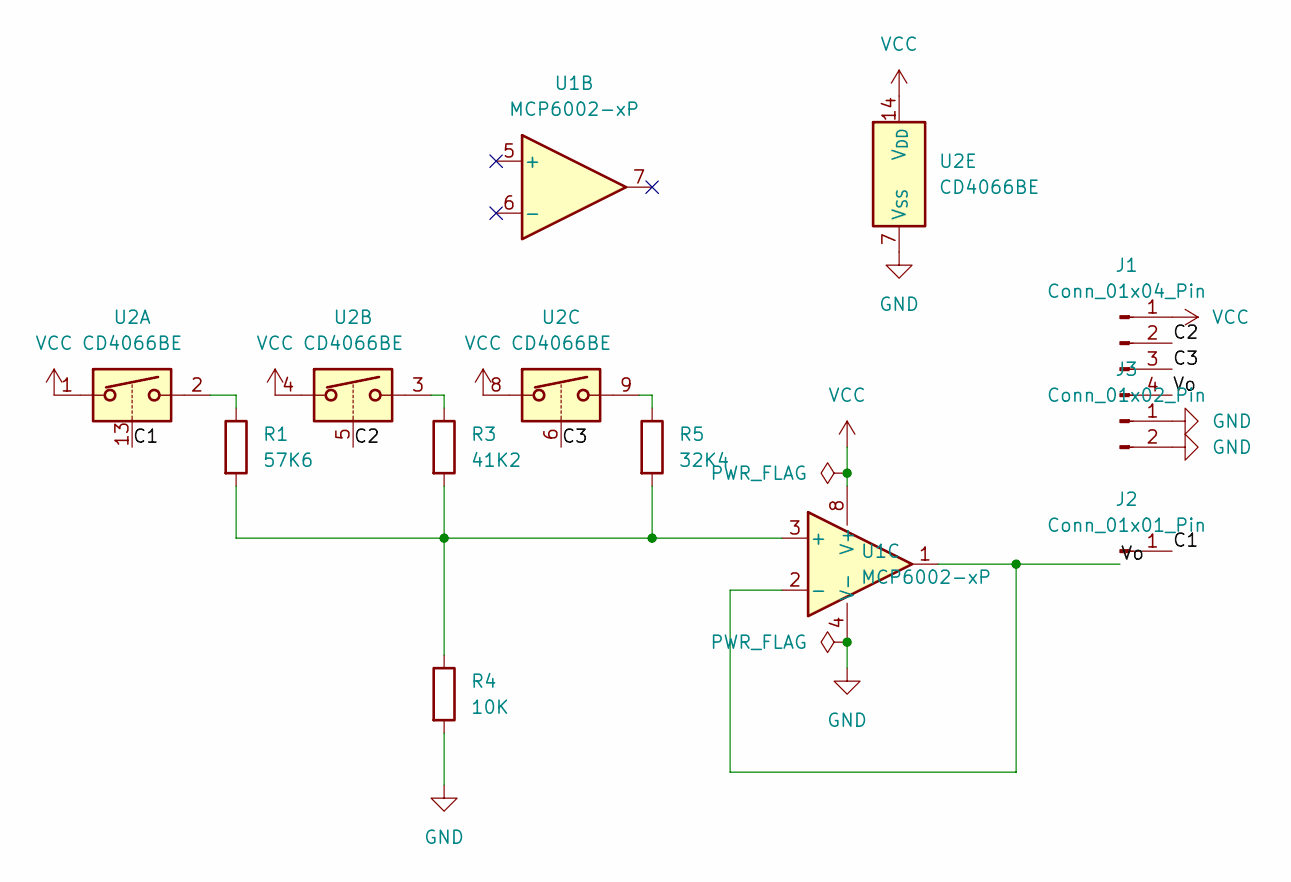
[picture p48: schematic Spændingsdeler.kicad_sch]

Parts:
J1: Conn_01x04_Pin; PinSocket_1x04_P2.54mm_Vertical
J2: Conn_01x01_Pin; PinSocket_1x01_P2.54mm_Vertical
J3: Conn_01x02_Pin; PinSocket_1x02_P2.54mm_Vertical
R1: 57K6; R_Axial_DIN0204_L3.6mm_D1.6mm_P7.62mm_Horizontal
R3: 41K2; R_Axial_DIN0204_L3.6mm_D1.6mm_P7.62mm_Horizontal
R4: 10K; R_Axial_DIN0204_L3.6mm_D1.6mm_P7.62mm_Horizontal
R5: 32K4; R_Axial_DIN0204_L3.6mm_D1.6mm_P7.62mm_Horizontal
U1: MCP6002-xP; DIP-8_W7.62mm_LongPads
U2: CD4066BE; DIP-14_W7.62mm_LongPads

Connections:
/C1: J2.1, U2.13
/C2: J1.2, U2.5
/C3: J1.3, U2.6
/Vo: J1.4, U1.1, U1.2 (-)
GND: J3.1, J3.2, R4.2, U1.4 (V-), U2.7 (V_{SS})
unnamed: R1.1, U2.2
unnamed: R3.1, U2.3
unnamed: R5.1, U2.9
unnamed: R1.2, R3.2, R4.1, R5.2, U1.3 (+)
VCC: J1.1, U1.8 (V+), U2.1, U2.4, U2.8, U2.14 (V_{DD})

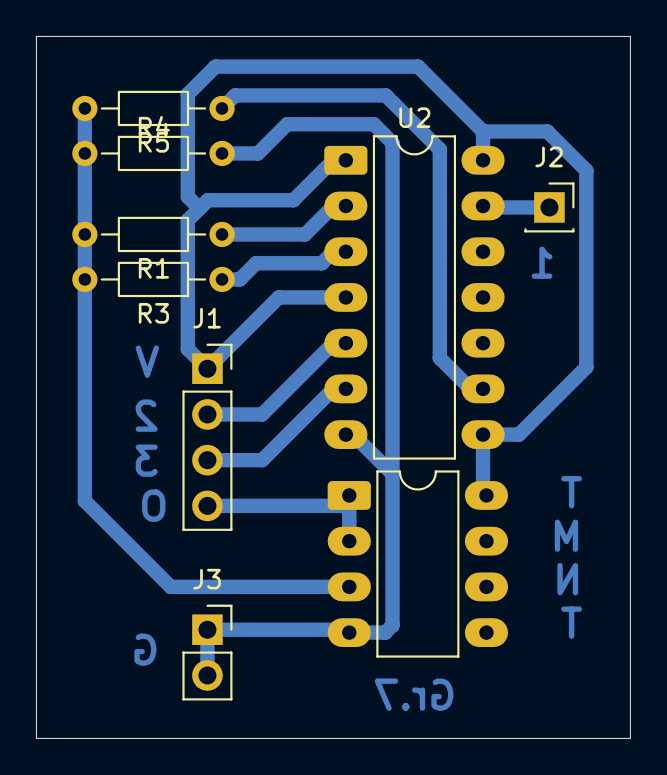
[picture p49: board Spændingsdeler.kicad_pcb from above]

Board: 2 copper layers, 33.0 x 39.0 mm, 9 parts (0 on the bottom side), 10 nets.

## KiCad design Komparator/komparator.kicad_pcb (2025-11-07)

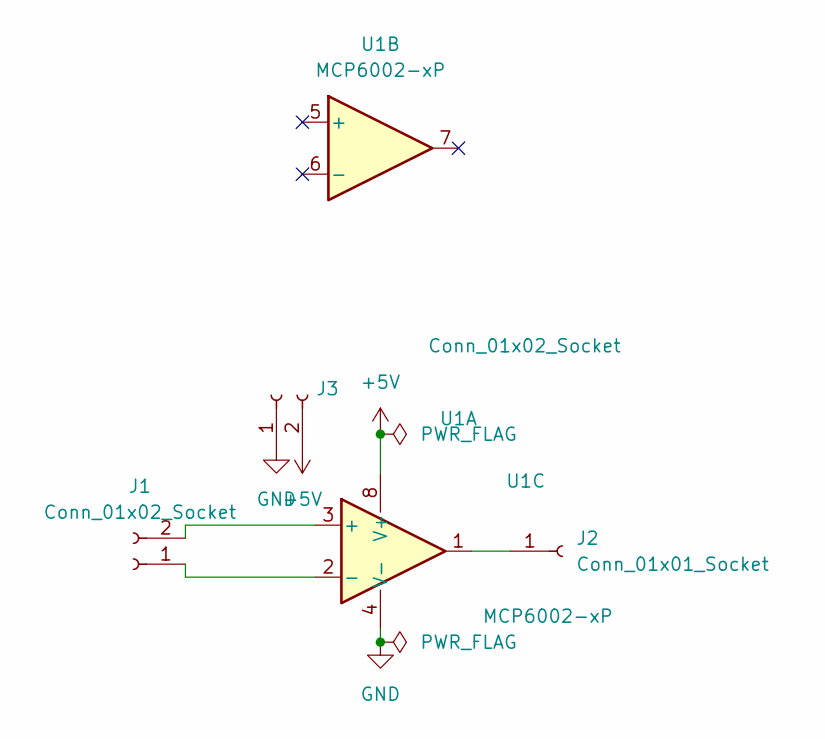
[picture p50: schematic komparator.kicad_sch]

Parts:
J1, J3: Conn_01x02_Socket; PinSocket_1x02_P2.54mm_Vertical
J2: Conn_01x01_Socket; PinSocket_1x01_P2.54mm_Vertical
U1: MCP6002-xP; DIP-8_W7.62mm_Socket

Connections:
+5V: J3.2, U1.8 (V+)
GND: J3.1, U1.4 (V-)
unnamed: J1.1, U1.2 (-)
unnamed: J1.2, U1.3 (+)
unnamed: J2.1, U1.1

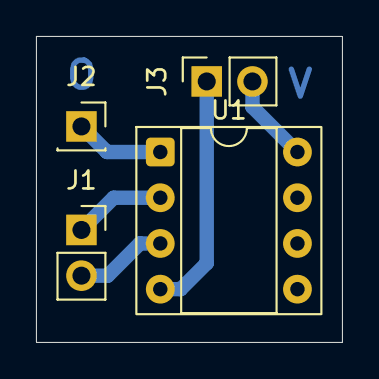
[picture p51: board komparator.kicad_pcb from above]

Board: 2 copper layers, 17.0 x 17.0 mm, 4 parts (0 on the bottom side), 5 nets.

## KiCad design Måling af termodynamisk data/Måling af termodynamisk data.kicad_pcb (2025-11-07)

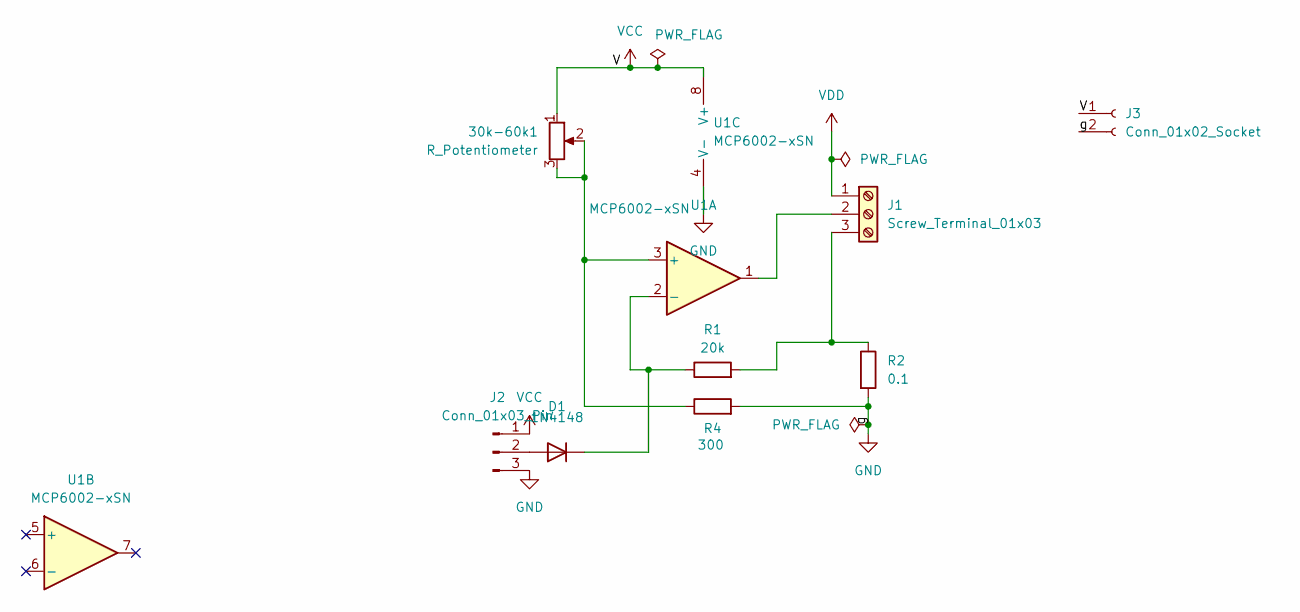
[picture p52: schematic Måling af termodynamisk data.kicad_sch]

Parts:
30k-60k1: R_Potentiometer; Potentiometer_ACP_CA9-V10_Vertical
D1: 1N4148; D_DO-35_SOD27_P7.62mm_Horizontal
J1: Screw_Terminal_01x03; TerminalBlock_bornier-3_P5.08mm
J2: Conn_01x03_Pin; PinHeader_1x03_P2.54mm_Vertical
J3: Conn_01x02_Socket; PinHeader_1x02_P2.54mm_Vertical
R1: 20k; R_Axial_DIN0204_L3.6mm_D1.6mm_P7.62mm_Horizontal
R2: 0.1; R_Axial_DIN0204_L3.6mm_D1.6mm_P7.62mm_Horizontal
R4: 300; R_Axial_DIN0204_L3.6mm_D1.6mm_P7.62mm_Horizontal
U1: MCP6002-xSN; DIP-8_W7.62mm_LongPads

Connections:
GND: J2.3, J3.2, R2.2, R4.2, U1.4 (V-)
unnamed: D1.2 (A), J2.2
unnamed: D1.1 (K), R1.1, U1.2 (-)
unnamed: J1.2, U1.1
unnamed: J1.3, R1.2, R2.1
unnamed: 30k-60k1.2, 30k-60k1.3, R4.1, U1.3 (+)
VCC: 30k-60k1.1, J2.1, J3.1, U1.8 (V+)
VDD: J1.1


Board: 2 copper layers, 31.0 x 39.0 mm, 9 parts (0 on the bottom side), 7 nets.

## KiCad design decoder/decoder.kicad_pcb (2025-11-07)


Board: 2 copper layers, 63.5 x 73.0 mm, 23 parts (0 on the bottom side), 25 nets.

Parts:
D1, D2, D3, D4, D5, D6, D7, D8, D9, D10, D11, D12, D13, D14, D15, D16: 1N4148WT; D_DO-35_SOD27_P7.62mm_Horizontal
J1: Conn_01x04_Socket; PinSocket_1x04_P2.54mm_Vertical
J2, J3: Conn_01x01_Pin; PinHeader_1x01_P2.54mm_Vertical
R1, R2: R; R_Axial_DIN0204_L3.6mm_D1.6mm_P7.62mm_Horizontal
U2, U3: 74HC238; DIP-16_W7.62mm_LongPads

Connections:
GND: R1.2, R2.2, U2.4 (~E1), U2.5 (~E2), U2.8 (GND), U3.4 (~E1), U3.8 (GND)
unnamed: D1.2 (A), U2.7 (Y7)
unnamed: D1.1 (K), D2.1 (K), D3.1 (K), D4.1 (K), D5.1 (K), D6.1 (K), D7.1 (K), D8.1 (K), J2.1
unnamed: D2.2 (A), U2.9 (Y6)
unnamed: D3.2 (A), U2.10 (Y5)
unnamed: D4.2 (A), U2.11 (Y4)
unnamed: D5.2 (A), U2.12 (Y3)
unnamed: D6.2 (A), U2.13 (Y2)
unnamed: D7.2 (A), U2.14 (Y1)
unnamed: D8.2 (A), U2.15 (Y0)
unnamed: D9.2 (A), U3.15 (Y0)
unnamed: D10.2 (A), U3.14 (Y1)
unnamed: D9.1 (K), D10.1 (K), D11.1 (K), D12.1 (K), D13.1 (K), D14.1 (K), D15.1 (K), D16.1 (K), R1.1
unnamed: D11.2 (A), U3.13 (Y2)
unnamed: D12.2 (A), U3.12 (Y3)
unnamed: D13.2 (A), U3.11 (Y4)
unnamed: D14.2 (A), U3.10 (Y5)
unnamed: D15.2 (A), U3.9 (Y6)
unnamed: D16.2 (A), U3.7 (Y7)
unnamed: J1.1, U2.1 (A0), U3.1 (A0)
unnamed: J1.2, U2.2 (A1), U3.2 (A1)
unnamed: J1.3, U2.3 (A2), U3.3 (A2)
unnamed: J1.4, U2.6 (E3), U3.5 (~E2)
unnamed: J3.1, R2.1
VCC: U2.16 (VCC), U3.6 (E3), U3.16 (VCC)

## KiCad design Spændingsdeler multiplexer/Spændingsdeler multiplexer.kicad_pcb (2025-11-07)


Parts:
J2: Conn_01x08_Pin; PinSocket_1x08_P2.54mm_Vertical
R1: 90K9; R_Axial_DIN0204_L3.6mm_D1.6mm_P7.62mm_Horizontal
R2, R4, R6: 10K; R_Axial_DIN0204_L3.6mm_D1.6mm_P7.62mm_Horizontal
R3: 61K9; R_Axial_DIN0204_L3.6mm_D1.6mm_P7.62mm_Horizontal
R5: 45K3; R_Axial_DIN0204_L3.6mm_D1.6mm_P7.62mm_Horizontal
U1: CD4066BE; DIP-14_W7.62mm_LongPads

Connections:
+5V: J2.1, R1.1, R3.1, R5.1, U1.14 (V_{DD})
/SpT1: J2.4, U1.2
/SpT2: J2.5, U1.3
/SpT3: J2.8, U1.9
/T1: J2.3, U1.13
/T2: J2.6, U1.5
/T3: J2.7, U1.6
GND: J2.2, R2.2, R4.2, R6.2, U1.7 (V_{SS})
unnamed: R1.2, R2.1, U1.1
unnamed: R3.2, R4.1, U1.4
unnamed: R5.2, R6.1, U1.8


Board: 2 copper layers, 49.0 x 40.0 mm, 8 parts (0 on the bottom side), 11 nets.

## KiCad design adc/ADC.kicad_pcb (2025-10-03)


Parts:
C1: 150nF; C_Axial_L3.8mm_D2.6mm_P7.50mm_Horizontal
J1: Conn_01x02_Pin; PinHeader_1x02_P2.54mm_Vertical
J2: Conn_01x01_Socket; PinSocket_1x01_P2.54mm_Vertical
J3: Conn_01x01_Pin; PinHeader_1x01_P2.54mm_Vertical
J4: Conn_01x08_Socket; PinSocket_1x08_P2.54mm_Vertical
R1: 100k; R_Axial_DIN0204_L3.6mm_D1.6mm_P7.62mm_Horizontal
U1: ADC0804LCN; DIP-20_W7.62mm_LongPads; MPN ADC0804LCN

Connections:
5V: J1.1, U1.20 (VCC)
GND: C1.1, J1.2, U1.1 (~CS), U1.2 (~RD), U1.7 (VIN(-)), U1.8 (AGND), U1.10 (DGND)
unnamed: J2.1, U1.6 (VIN(+))
unnamed: J3.1, U1.3 (~WR)
unnamed: J4.1, U1.18 (DB0)
unnamed: J4.2, U1.17 (DB1)
unnamed: J4.3, U1.16 (DB2)
unnamed: J4.4, U1.15 (DB3)
unnamed: J4.5, U1.14 (DB4)
unnamed: J4.6, U1.13 (DB5)
unnamed: J4.7, U1.12 (DB6)
unnamed: J4.8, U1.11 (DB7)
unnamed: R1.1, U1.4 (CLK_IN)
unnamed: C1.2, R1.2, U1.19 (CLK_R)


Board: 2 copper layers, 27.5 x 37.5 mm, 7 parts (0 on the bottom side), 14 nets.

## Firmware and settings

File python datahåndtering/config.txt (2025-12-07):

in: ovn9.csv
out: maxmin 50C
iscale: 0.001
oscale: 0.001
start: 304
end: 381
oo: csv,svg
yscale: 0.01,1
xlabel: tid[s]
ylabel: temp[C],Volt
curves: Ovn-Temp,Komperator

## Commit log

2025-09-12 tilføj opgave 1 og 2 fra lektion 1
    [digital oscilatoropgave 2.kicad_pcb, digital oscilatoropgave 2.kicad_sch, tester-B_Cu.dxf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]
2025-09-19 maple til ovn projekt og schematic
    [digital oscilatoropgave 2.kicad_sch]
2025-09-19 schematic og pcb er færdig nr 1
    [digital oscilatoropgave 2.kicad_pcb, digital oscilatoropgave 2.kicad_sch]
2025-09-19 første dxf fil til print af oscillator
    [digital oscilatoropgave 2-B_Cu.dxf, digital oscilatoropgave 2.kicad_pcb]
2025-09-26 ryttet op og tilføjet excel document til termodynamisk arametre
    [regnemaskine til R3 udfra ønsket effekt.xlsx]
2025-09-26 maple pdf
    [regnemaskine til R3 udfra ønsket effekt.xlsx, tester-B_Cu.dxf, tester-Edge_Cuts.dxf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]
2025-09-26 tester ting
    [tester-B_Cu.dxf, tester.kicad_pcb]
2025-09-26 termodynamik schematic og pcb
    [Måling af termodynamisk data-B_Cu.dxf, Måling af termodynamisk data.kicad_pcb, Måling af termodynamisk data.kicad_sch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]
2025-09-26 ting og sager
    [Måling af termodynamisk data.kicad_pcb, Måling af termodynamisk data.kicad_sch, digital oscilatoropgave 2.kicad_pcb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]
2025-10-01 digital oscillator færdig
    [digital oscilatoropgave 2.kicad_pcb, digital oscilatoropgave 2.kicad_sch]
2025-10-03 start af adc og decoder
    [ADC og decoder.kicad_pcb, ADC og decoder.kicad_sch, ADC.kicad_sch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]
2025-10-03 start af adc og decoder (fix)
2025-10-03 datablade til adc og decoder
2025-10-03 decoder færdig
    [decoder-B_Cu.dxf, decoder.kicad_pcb, decoder.kicad_sch]
2025-10-03 adc færdig
    [ADC-B_Cu.dxf, ADC.kicad_pcb, ADC.kicad_sch]
2025-10-03 lidt forskelligt
    [Måling af termodynamisk data.kicad_pcb, Måling af termodynamisk data.kicad_sch, decoder.kicad_pcb]
2025-10-22 måling af termodynamisk måling forhåbentlig færdig for tredje gang
    [Måling af termodynamisk data-B_Cu.dxf, Måling af termodynamisk data.kicad_pcb, Måling af termodynamisk data.kicad_sch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]
2025-10-24 tilføjet differensforstærker kicad
    [Differensforstærker.kicad_pcb, Differensforstærker.kicad_sch]
2025-10-29 komparator upd.
    [komparator.kicad_pcb]
2025-10-29 differens forstærker- de sidste udregninger og pcb
    [Differens forstærker-B_Cu.dxf, Differens forstærker-Edge_Cuts.dxf, Differens forstærker.kicad_pcb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]
2025-10-31 komp mappestruktur
    [komparator.kicad_pcb, komparator.kicad_sch]
2025-10-31 spændingsdeler pcb med DXF
    [Spændingsdeler-B_Cu.dxf, Spændingsdeler.kicad_pcb, Spændingsdeler.kicad_sch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]
2025-10-31 spændingsdeler små ting
    [Spændingsdeler-B_Cu.dxf, Spændingsdeler.kicad_pcb]
2025-10-31 differens forstærker små fix
    [Differens forstærker-B_Cu.dxf, Differens forstærker.kicad_pcb]
2025-10-31 bom til komerator
2025-11-03 DXF til differens forstærker og komperator
    [regnemaskine til R3 udfra ønsket effekt.xlsx]
2025-11-09 start af hele ovnstyringen på et pcb
    [adc.kicad_sch, afv-display.kicad_sch, dif-forstærker.kicad_sch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]
2025-11-12 spændingsfølger i spændingsdeleren
    [ovn driver.kicad_sch, samlet pcb.kicad_sch, spv.kicad_sch]
2025-11-14 tilstandsmaskine er noget tis
    [digital styring.ods]
2025-11-14 tilstandsmaskine er noget tis #2
    [digital styring.kicad_pcb, digital styring.kicad_sch, digital styring.ods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]
2025-11-21 digital styring pcb færdig(?)
    [digital styring-B_Cu.dxf, digital styring-F_Cu.dxf, digital styring.kicad_pcb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]
2025-11-27 tis 3
    [digital styring.ods]
2025-11-27 finpudsning decoder
    [decoder til tilstand.kicad_sch]
2025-11-27 digital styring FÆRDIG
    [digital styring.kicad_sch, digital styring.ods, input.kicad_sch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]
2025-11-28 datahåndtering ting
    [out.csv, small.csv, termo.ods]
2025-12-02 python datahåndtering meget bedre
    [config.txt, tis5-out.csv]
2025-12-03 python datahåndtering flere y akser næsten done
    [config.txt]
2025-12-03 python datahåndtering er helt færdig
    [config.txt, merged_tis2-out.csv]
2025-12-05 Projekt er færdig!!!
    [config.txt, digital styring.ods, ovn0-fjernet tid-out.csv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]
2025-12-07 alt muligt
    [config.txt, digital styring.kicad_sch, grader_pr_sekund.csv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]
